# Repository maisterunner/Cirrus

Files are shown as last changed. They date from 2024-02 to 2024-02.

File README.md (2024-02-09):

# Cirrus
Low-cost PCB for flight control and logging purposes for small UAV-s

For PCB design learning, and embedded programming

EasyEDA was used for the eCAD work

## V1

### Pinout

- STM32F103 microprocessor for control
- 12 MHz chrystal resonator (does not work on finished PCB)
- Debug tagconnector
- 5V to 3V3 LDO (AMS1117) for supply
- CAN transciever for the possibility to use multiple controllers in one vehicle to split up the tasks
- 6 PWM outputs for servo control
- 2 I2C interfaces exposed for connecting sensors
- 2 SPI interfaces exposed for connecting sensors
- 1 UART interface exposed for connecting sensors
- 1 ADC exposed for measurements (current etc.)
- PA4, PA12, PB1, PC15 exposed to be used as GPIO (interrupt pin)

### Interfaces
Interfaces exposed with pads for soldered wired connections.

### Manufacturing
4 layers with signal-ground-ground-signal

One sided assembly

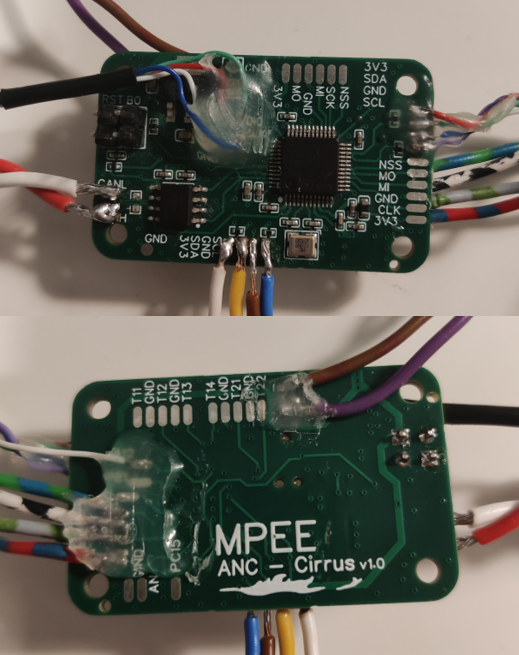
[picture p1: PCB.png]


## V2

### Pinout

- STM32L431 -> for more interrupts and DMAs
- 16MHz chrystal resonator (issues fixed)
- Debug changed for pads
- 6 PWM added 5V rail for power
- Power LEDs added
- User LEDs added

### Interfaces
Connection pads made smaller (made it very challenging to solder by hand)

Form factor changed to include two mounting holes aligned with conventional 30.5mm x 30.5mm flight controller pattern.

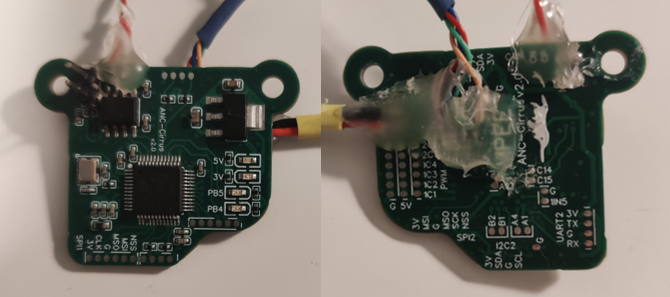
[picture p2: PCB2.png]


## V3

### Pinout

- STM32G431 -> for higher clock speed and more adc features
- Possibility for fast trigonometric calculations (CORDIC)
- Possibility for filter acceleration (FMAC)
- Added user buttons
- Analog interfaces with OPAMP

### Interfaces
Connection pads exchanged for JST SMD (1mm) connectors.
Vertical JST SMD (2.54mm) added for servo connection.
Bottom side received the possibility for a daughter SMPS board to be able to receive 8-36V and provide the board with 5V power.

### Manufacturing
Assembly is still on top side by PCB manufacturer. Bottom side components added but only components that can be soldered by hand.

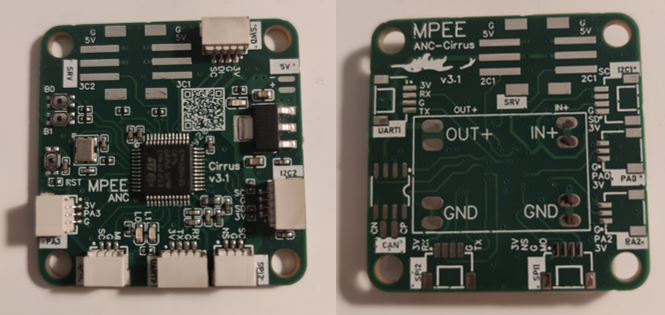
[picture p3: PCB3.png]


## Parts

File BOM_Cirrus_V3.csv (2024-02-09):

ID | Name | Designator | Footprint | Quantity | Manufacturer Part | Manufacturer | Supplier | Supplier Part | Price
1 | JST_SMD_VERT_3p | U8,U9,U6,U7 | JST_SMD_3P | 4
2 | 1.0K-BH-3PWB | CN2,CN1,CN8,CN9,CN10 | CONN-SMD_3P-P1.00_HDGC_1.0K-BH-3PWB | 5 | 1.0K-BH-3PWB | HDGC(华德共创) | LCSC | C2919604 | 0.042
3 | 1.0-4PWB | CN6,CN12,CN3,CN4,CN7,CN5,CN11 | CONN-SMD_4P-P1.00_DEALON_1.0-4PWB | 7 | 1.0-4PWB | DEALON(德艺隆) | LCSC | C2905006 | 0.035
4 | 2p_smd_connector | U3,U2 | 2P_SMD_CONNECTOR | 2
5 | TJA1050T/CM,118 | U1 | SOIC-8_L5.0-W4.0-P1.27-LS6.0-BL | 1 | TJA1050T/CM,118 | NXP(恩智浦) | LCSC | C6952 | 0.899
6 | DC-DC step-down breakout | U11 | BUCK PSU BREAKOUT | 1
7 | 100nF | C1,C2,C12,C13,C14,C15,C7 | C0402 | 7 | CL05B104KO5NNNC | SAMSUNG(三星) | LCSC | C1525 | 0.001
8 | 10uF | C11 | C0402 | 1 | CL05A106MQ5NUNC | SAMSUNG(三星) | LCSC | C15525 | 0.005
9 | 600Ω | L1 | L0603 | 1 | GZ1608D601TF | Sunlord(顺络) | LCSC | C1002 | 0.005
10 | YELLOW | LED1,LED2,LED_PWR1 | LED0603-RD-YELLOW | 3 | 19-213/Y2C-CQ2R2L/3T(CY) | EVERLIGHT(亿光) | LCSC | C72038 | 0.022
11 | 10K | R5 | R0402 | 1 | 0402WGF1002TCE | UNI-ROYAL(厚声) | LCSC | C25744 | 0.001
12 | 1TS028A-1800-0600-CT | SW1,SW2,SW3 | SW-SMD_4P-L2.8-W1.9-P1.20-LS3.0_1TS028A | 3 | 1TS028A-1800-0600-CT | HYP(鸿源精密) | LCSC | C481988 | 0.078
13 | 16Mhz | X1 | OSC-SMD_4P-L3.2-W2.5-BL | 1 | X3Z016000B91H-U | HELE(台湾加高) | LCSC | C254221 | 0.441
14 | 22uF | C3,C4 | C0603 | 2 | GRM188B30J226MEA0D | muRata(村田) | LCSC | C15500 | 0.194
15 | 10pF | C5,C6 | C0402 | 2 | CL05C100JB5NNNC | SAMSUNG(三星) | LCSC | C32949 | 0.006
16 | 1uF | C8,C10 | C0402 | 2 | CL05A105KA5NQNC | SAMSUNG(三星) | LCSC | C52923 | 0.004
17 | 10nF | C9 | C0402 | 1 | CL05B103KB5NNNC | SAMSUNG(三星) | LCSC | C15195 | 0.001
18 | 2.2kΩ | R1,R2,R3,R4,R7,R8 | R0402 | 6 | 0402WGF2201TCE | UNI-ROYAL(厚声) | LCSC | C25879 | 0.001
19 | 1kΩ | R6,R9,R10 | R0402 | 3 | 0402WGF1001TCE | UNI-ROYAL(厚声) | LCSC | C11702 | 0.001
20 | 22Ω | U4 | R0402 | 1 | HPCR0402F22R0K9 | RESI(开步睿思） | LCSC | C364973
21 | AMS1117-3.3 | U5 | SOT-223-3_L6.5-W3.4-P2.30-LS7.0-BR | 1 | AMS1117-3.3 | AMS | LCSC | C6186 | 0.141
22 | STM32G431CBT6 | U10 | LQFP-48_L7.0-W7.0-P0.50-LS9.0-BL | 1 | STM32G431CBT6 | ST(意法半导体) | LCSC | C529355 | 3.104

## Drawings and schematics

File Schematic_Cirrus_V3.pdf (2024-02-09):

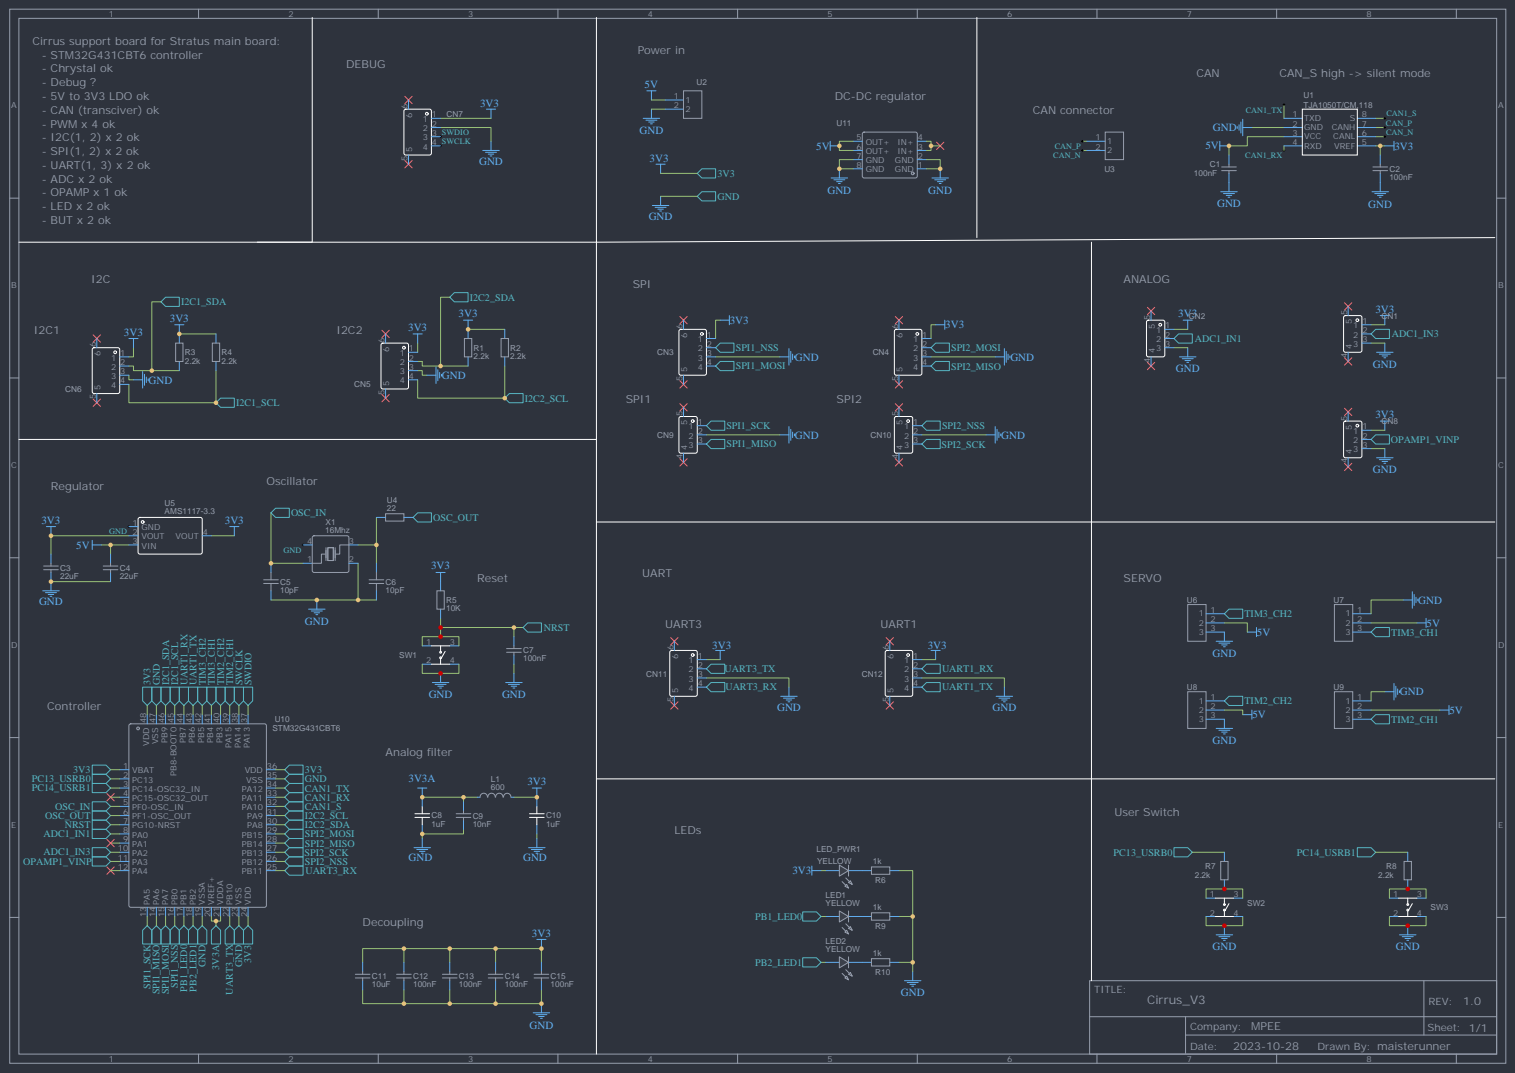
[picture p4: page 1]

Cirrus support board for Stratus main board:
- STM32G431CBT6 controller
- Chrystal ok
- Debug ?
- 5V to 3V3 LDO ok
- CAN (transciver) ok
- PWM x 4 ok
- SPI(1, 2) x 2 ok
- UART(1, 3) x 2 ok
- ADC x 2 ok
- OPAMP x 1 ok

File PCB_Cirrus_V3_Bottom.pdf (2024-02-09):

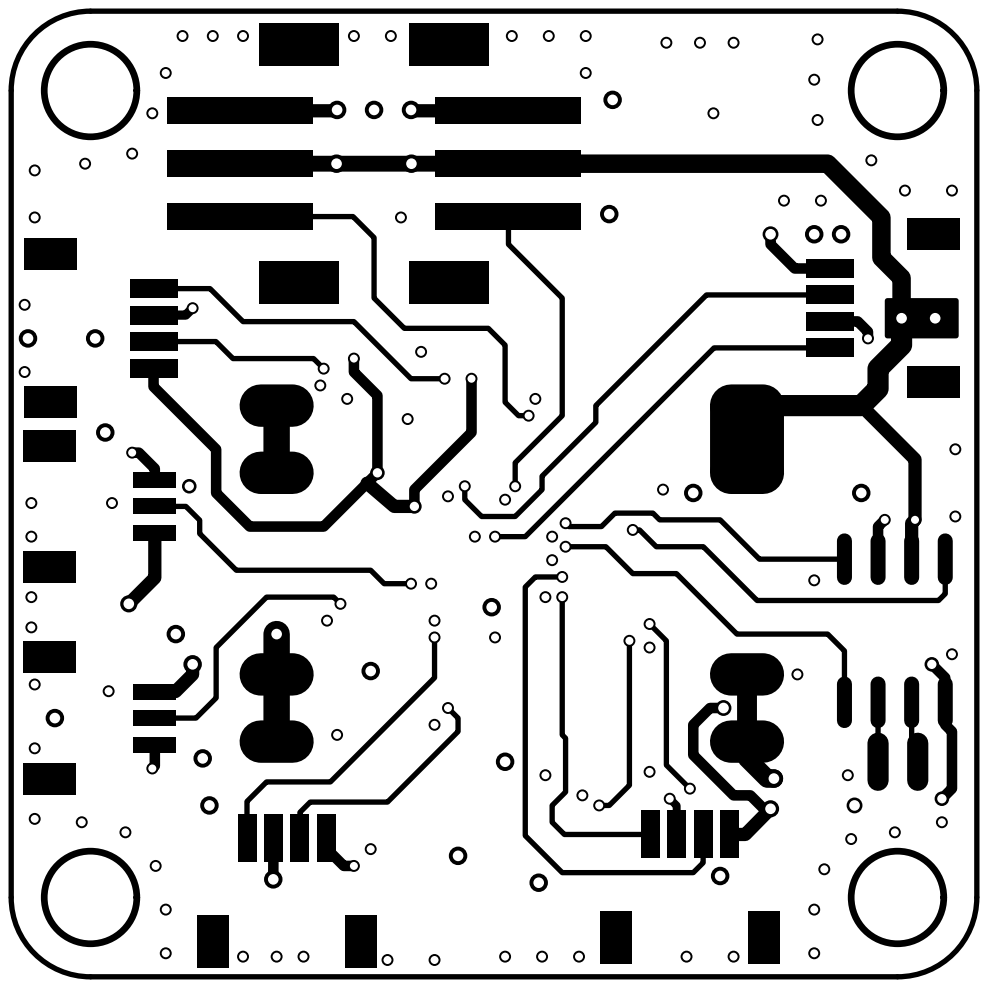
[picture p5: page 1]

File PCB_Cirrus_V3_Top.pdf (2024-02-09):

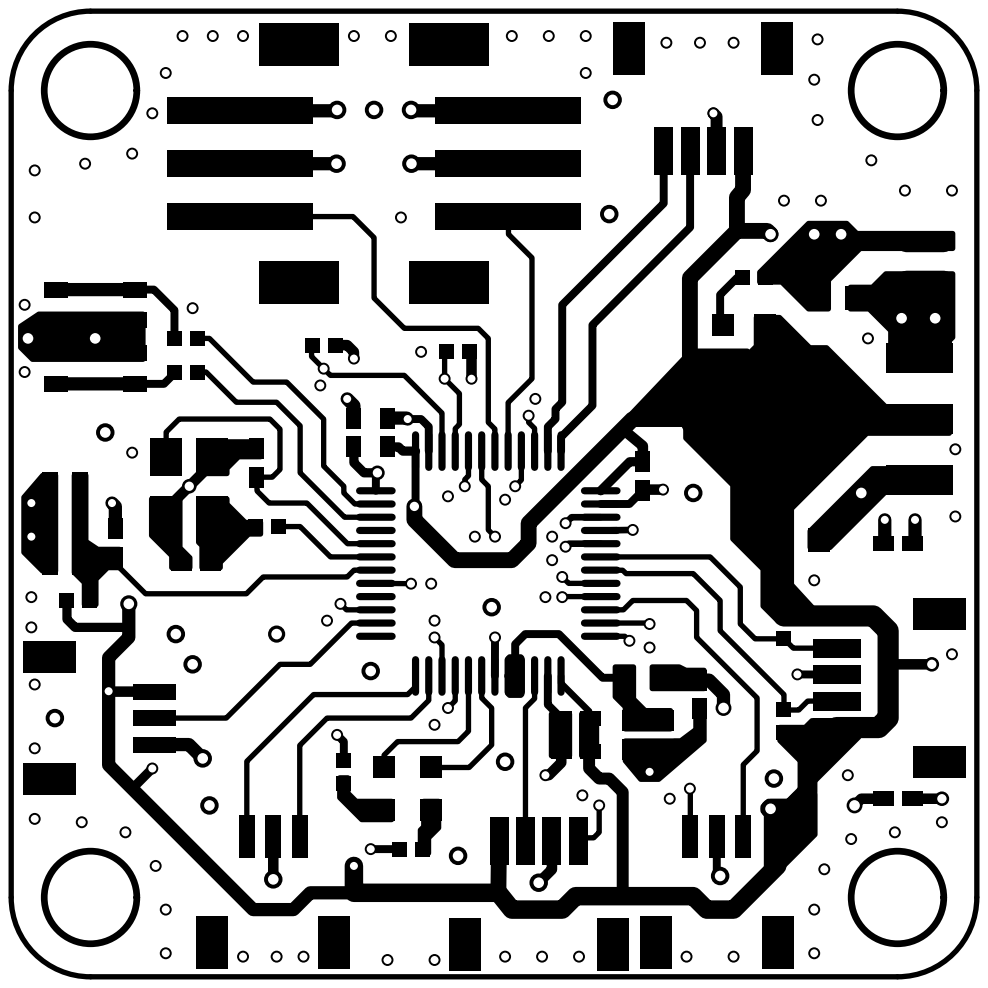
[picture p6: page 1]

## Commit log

2024-02-04 Cirrus V1
    [BOM_F103C8-Cirrus.csv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]
2024-02-05 Cirrus V2
    [BOM_F103C8-Cirrus.csv, BOM_L431-CirrusV2.csv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]
2024-02-09 Cirrus V3
    [BOM_Cirrus_V3.csv, BOM_L431-CirrusV2.csv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]
